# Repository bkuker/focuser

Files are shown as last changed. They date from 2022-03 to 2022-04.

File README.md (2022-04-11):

# Focuser

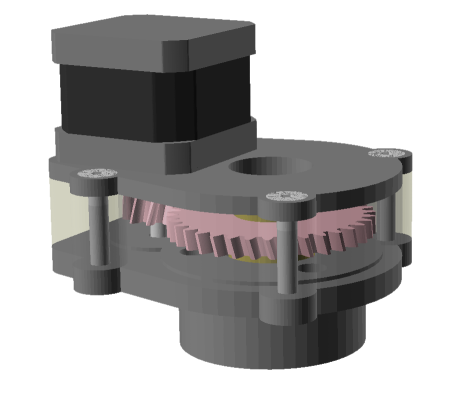
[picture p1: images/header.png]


A 3d printable focuser for Celestron 11" and Moonlite compatible firmware for arduino.

# Hardware

3d Printable, requires NEMA 17 stepper & m3 screws, 30mm M5 flat head screws, thin m5 nuts nuts.

Prints in 6 parts with no support. top and bottom are each printed in two parts and glued together. The only overhangs are the countersinks on top, they print reliably with no support. For all parts I suggest hotter than normal bed temp (70C for PLA) and no brim. Set the printer to leave the bed hot when done, and cover the part with something insulating like a hand towel before turning off the bed heat. Letting the part soak up the heat from the bed, followed by slow even cooling, zero warpage!

# Software

Adapted from https://www.andico.org/2014/04/arduino-based-motor-focuser-controller.html

I forget what I changed and why.

# Libraries

The following libraries are used:

* AccelStepper by Mike McCauley
* NopSCADlib
* Gears Library for OpenSCAD by janssen86.

They are included in this repo for ease of use.

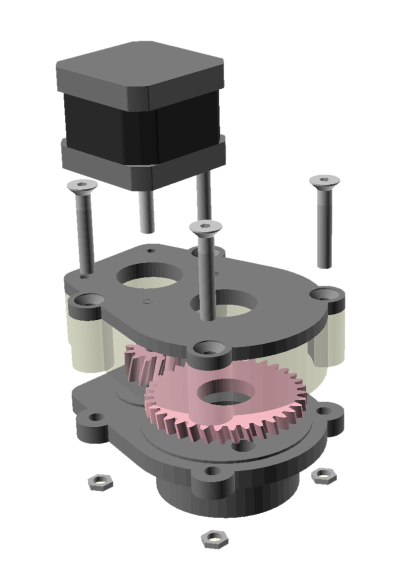
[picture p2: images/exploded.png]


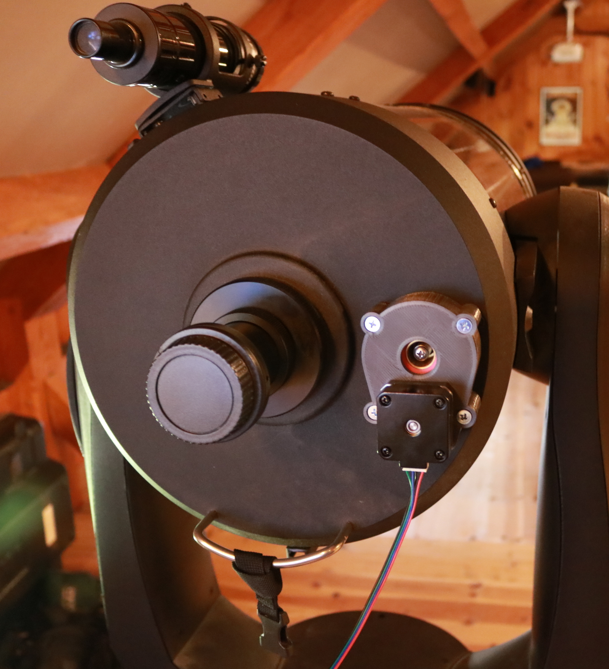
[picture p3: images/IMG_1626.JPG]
In Use


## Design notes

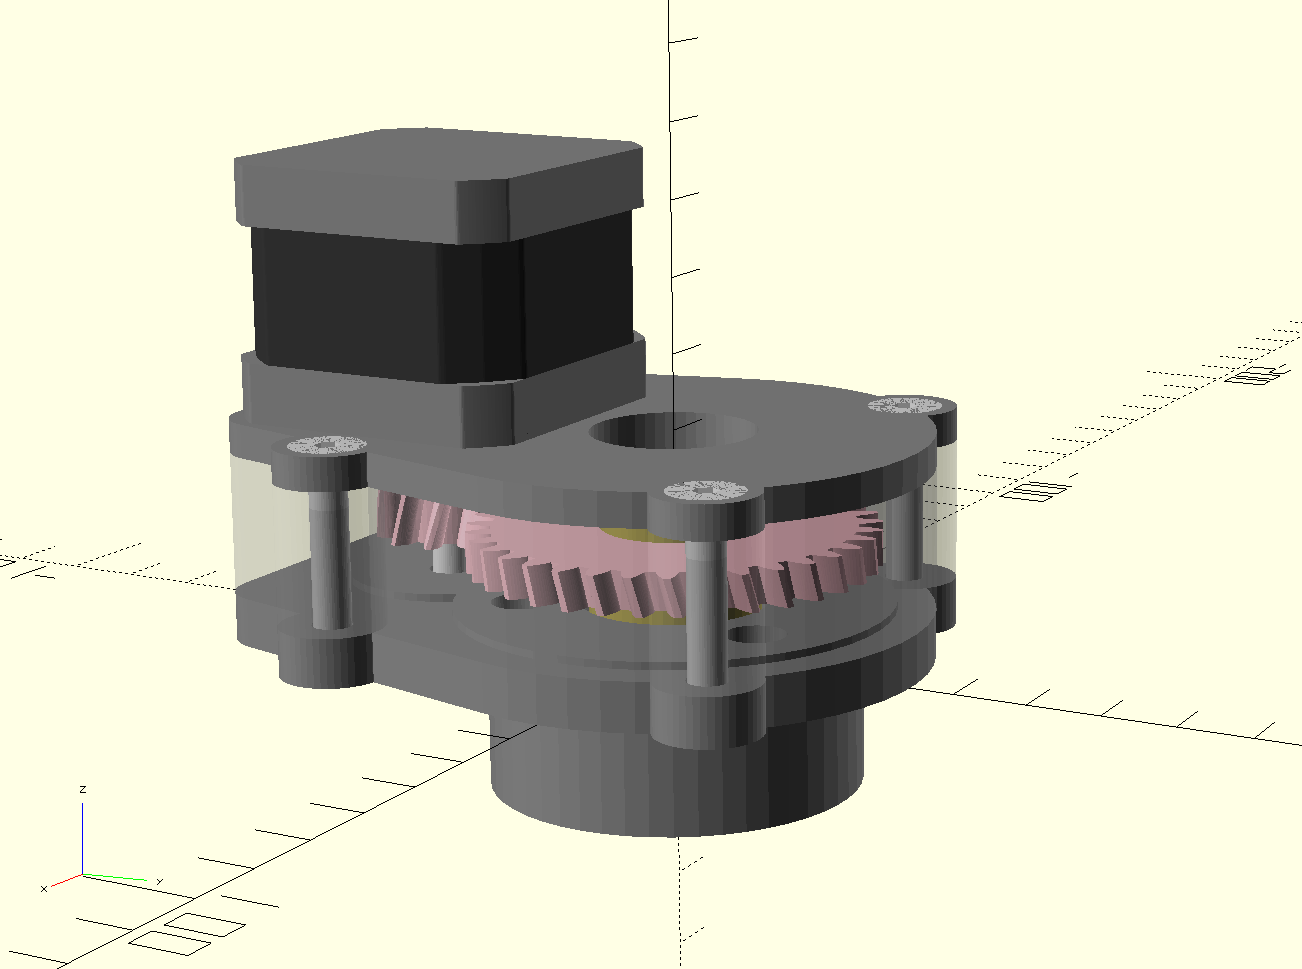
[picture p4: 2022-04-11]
images/Screenshot 2022-04-11 095923.png

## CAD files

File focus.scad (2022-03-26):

include <libraries/NopSCADlib-e5a38b37b3bf3278dea1beb750950f22401af77d/lib.scad>
include <libraries/gears/gears.scad>

NEMA17SB = ["NEMA17S", 42.3, 20, 53.6/2, 25, 11, 2, 5, 20, 31, [8, 8], 3, false, false, 0, 0];

module bosses(){
    //translate([27,20,0])
        //children();
    translate([-27,20,0])
        children();
    translate([27,-35,0])
        children();
}

module screws(){
    translate([0,0,30]){
        bosses(){
            screw(M5_cs_cap_screw, 30);
            translate([0,0,-30])
                scale([1,1,.5])
                    nut(M5_nut);
        }
    }
}

module screws_clearance(){
    translate([0,0,30]){
        bosses(){
            translate([0,0,-.1])
                screw_countersink(M5_cs_cap_screw, drilled = false);
            translate([0,0,.1])
                screw_countersink(M5_cs_cap_screw, drilled = false);
            translate([0,0,-32])
                cylinder(35,2.55,2.55);
            translate([0,0,-31.5])
                    nut(M5_nut);
        }
    }
}

t=4;
module outside(){
    union(){
        bosses(){
            cylinder(1, 7, 7, false);
        }
        hull(){
            cylinder(1, 30+t, 30+t, false);
            translate([0,-34.9,0]){
                cylinder(1, 12+t, 12+t, false);
                rotate([0,0,180])
                    NEMA_screw_positions(NEMA17SB, n = 2)
                        cylinder(1,7,7);
            }
        }
    }
}

module inside(){
    union(){
       cylinder(1, 29.5, 29.5, false);
        translate([0,-34.9,0])
            cylinder(1, 14, 14, false);
    }
}


module base(){
    difference(){
        scale([1,1,6.5])
            outside();

        translate([0,0,-1]){
            cylinder(3.5, 49/2, 49/2, false);
            for ( a = [0, 120, 240] )
                rotate([0,0,a])
                    translate([-20,0,0])
                        cylinder(50, 2,2, true);
            cylinder(50, 25/2,25/2, true);
        }

        screws_clearance();
        
        translate([0,-34.9,0-1]){
            cylinder(50, 3, 3, true);
        }
    }
}

module shell(){
    difference(){
        translate([0,0,6.5])
            scale([1,1,19])
                outside();
        
        scale([1,1,27])
            inside();
        
        screws_clearance();
    }
}

module top(){
    difference(){
        translate([0,0,25.5]){
            difference(){
                union(){
                    scale([1,1,4.5])
                        outside();
                    translate([0,0,-1])
                        inside();
                }
                translate([0,-34.9,4.5]){
                    rotate([0,180,0]){
                        NEMA(NEMA17SB);
                        cylinder(10,NEMA_big_hole(NEMA17SB)+.1,NEMA_big_hole(NEMA17SB)+.1);
                        NEMA_screw_positions(NEMA17SB, n = 4)
                            cylinder(5,1.7,1.7);
                        translate([0,0,3])
                            NEMA_screw_positions(NEMA17SB, n = 4)
                                cylinder(5,4,4);
                    }
                }
                translate([0,0,-2])
                    cylinder(20,11,11);
            }
        }
        screws_clearance();
    }
}

module hardware(){
    translate([0,0,25.5])
        translate([0,-34.9,4.5])
            rotate([0,180,180])
                NEMA(NEMA17S);
    screws();
    color("#b5a642"){
        union(){
            cylinder(12.5, 22.5/2, 22.5/2, false);
            cylinder(20, 19.5/2, 19.5/2, false);
        }
    }
}




module gears(){
    ha = 20;
    mod = 1.525;
    translate([0,0,12.5]){
        spur_gear (modul=mod, tooth_number=35, width=8, bore=19.5, pressure_angle=20, helix_angle=ha, optimized=false);
    }


    translate([0,-34.9,8.5]){
        rotate([0,0,16.5])
        spur_gear (modul=mod, tooth_number=11, width=15, bore=5, pressure_angle=20, helix_angle=-ha, optimized=false);
    }
}

*hardware();

*gears();

base();
color("cyan", .5){
    shell();
}
color("green", .5){
     top();
}



//pcb(ArduinoNano);

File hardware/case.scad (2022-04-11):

module electronics(){
    translate([0,0,1.4]){
        color("green")
            cube([31,70,2]);
            translate([2.3,70-43-2.5,13])
        color("blue")
            cube([18,43,1.5]);
        color("gray"){
            translate([2.3+18/2-8/2,60,14.5]){
                cube([8,10,4]);
            }
        }
    }
}

*electronics();

    t = 2;
    s=.5;

module case(){
        

    union(){
        difference(){
            translate([-(t+s),-(t+s),-t]){
                cube([33.5+2*s+t*2,70+2*s+t*2,24+t*2]);
            }
            translate([-s,-s,0])
            cube([33.5+2*s,70+2*s,24]);
            
            translate([2.3+18/2-11/2-.25,60,1.5+14.5-5/2-.5]){
                cube([11.5,20,10]);
            }
            
            translate([27, 80, 15])
                rotate([90,0,0])
                    cylinder(20,11.5/2,11.5/2);
            
            translate([(33.5+2*s+t*2)/2-(t+s),0,15])
                cube([12.5,20,6],true);
        }
        
        difference(){
            union(){
                translate([-s,-s,0])
                    cube([2,70,5]);
                translate([30-s*2,0,0])
                    cube([5,70,5]);
            }
            electronics();
        }
        
    }
}

intersection(){
    case();
    cube([100,100,100], true);
}

translate([0,20,0])
    difference(){
        case();
        cube([100,100,100], true);
    }

!translate([(33.5+2*s+t*2)/2-(t+s),-t-s-10,15]){
    difference(){
        rotate([90,0,0])
            cylinder(3,10,11.5/2);
        translate([0,0,-12])
            cube([5,10,20],true);
    }
}
    
    
    
    
    

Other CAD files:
hardware/focus.scad

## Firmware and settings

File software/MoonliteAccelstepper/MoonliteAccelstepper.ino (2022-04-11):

// Moonlite-compatible stepper controller
//
// Uses AccelStepper (http://www.airspayce.com/mikem/arduino/AccelStepper/)
//
// Requires a 10uf - 100uf capacitor between RESET and GND on the motor shield; this prevents the
// Arduino from resetting on connect (via DTR going low).  Without the capacitor, this sketch works
// with the stand-alone Moonlite control program (non-ASCOM) but the ASCOM driver does not detect it.
// Adding the capacitor allows the Arduino to respond quickly enough to the ASCOM driver probe
//
// orly.andico@gmail.com, 13 April 2014

#include "src/AccelStepper/AccelStepper.h"

#include <DallasTemperature.h>

/* Microstepping Settings.
 * Run full 16x microstepping all the time on hardware for smoothing and reducing resonance.
 * 
 * Multiply/devide commanded reported position by microsteps, so every 1 step from software results
 * in 16 microsteps. Driver is reset on startup to ensure we always stop on full steps. This makes
 * the position stay more stable when enabling / disabling the driver whild idle to reduce power
 * usage and stepper heat.
 */
#define MICROSTEPS 16
#define MICROSTEP_MULTIPLIER (half_step?MICROSTEPS:MICROSTEPS*2)

/* The gear ratio of the stepper to focuser. 3 means 3 stepper rotations to one focuser rotation */
#define GEAR_RATIO 3
/* How many steps per full revolution of the motor itself (not including gearing) */
#define NATIVE_STEPS_PER_REV 200
/* How many pulses of the STEP pin for one revolution of gear shaft */
#define STEPS_PER_REV (NATIVE_STEPS_PER_REV * GEAR_RATIO * MICROSTEPS)

/*How many seconds for one rotation of the output in full step mode*/
#define SECONDS_PER_REV 3
#define MAXSPEED (STEPS_PER_REV / SECONDS_PER_REV)
#define ACCELERATION 4000

/*How long wait after motion is stopped to disable stepper */
#define SETTLE_MS 500

/* Stepper pins */
#define DIR_PIN  2
#define STEP_PIN 3
#define ENABLE_PIN 6
#define RESET_PIN 5 //Optional

//Not used, but might be hooked to arduino for lazyness
#define MS3 7
#define MS2 8
#define MS1 9
#define SLEEP_PIN 4

/* Optional feature pins */
//#define ONE_WIRE_BUS 11
#define LED_PIN 10

AccelStepper stepper(1, STEP_PIN, DIR_PIN);

#ifdef ONE_WIRE_BUS
OneWire oneWire(ONE_WIRE_BUS); 
DallasTemperature sensors(&oneWire);
DeviceAddress thermometer;
#endif


//Input Handling
#define MAXCOMMAND 8
char inChar;
char cmd[MAXCOMMAND];
char param[MAXCOMMAND];
char line[MAXCOMMAND];
int eoc = 0;
int idx = 0;

//Internal State
int lastTemp = 0;
long millisLastTemp = 0;
long millisLastMove = 0;

//Moonlite State
long pos;
int speed = 2;
int half_step = 0;
int light = 255;

void setup()
{  
  Serial.begin(9600);
  
  stepper.setMaxSpeed(MAXSPEED);
  stepper.setAcceleration(ACCELERATION);
  stepper.disableOutputs();
  stepper.setEnablePin(ENABLE_PIN);
  stepper.setPinsInverted(true,false,true);
  memset(line, 0, MAXCOMMAND);
  millisLastMove = millis();

#ifdef LED_PIN
  analogWrite(LED_PIN, light);
#endif

  pinMode(MS1, OUTPUT);
  digitalWrite(MS1, HIGH);
  pinMode(MS2, OUTPUT);
  digitalWrite(MS2, HIGH);
  pinMode(MS3, OUTPUT);
  digitalWrite(MS3, HIGH);
  pinMode(SLEEP_PIN, OUTPUT);
  digitalWrite(SLEEP_PIN, HIGH);

  pinMode(LED_BUILTIN, OUTPUT);
  

#ifdef RESET_PIN
  //Reset driver and pulse it to align to a whole step
  pinMode(RESET_PIN, OUTPUT);
  digitalWrite(RESET_PIN, LOW);
  delay(10);
  digitalWrite(RESET_PIN, HIGH);
  delay(10);
  stepper.enableOutputs();
  delay(10);
  stepper.disableOutputs();
#endif

#ifdef ONE_WIRE_BUS
  //Start up sensors
  sensors.begin();
  sensors.getAddress(thermometer, 0);
  sensors.requestTemperaturesByAddress(thermometer);
  lastTemp = sensors.getTempC(thermometer)*2;
  sensors.setWaitForConversion(false);
#endif
}

void motion(){
  //Motion Controll
  if (stepper.run()) {
    millisLastMove = millis();
  } 
  else {
    // reported on INDI forum that some steppers "stutter" if disableOutputs is done repeatedly
    // over a short interval; hence we only disable the outputs and release the motor some seconds
    // after movement has stopped
    if ((millis() - millisLastMove) > SETTLE_MS) {
       stepper.disableOutputs();
    }
  }
}


void loop(){
  motion();

  if (stepper.run()) {
    digitalWrite(LED_BUILTIN, bitRead(millis(), 7));
  } else {
    digitalWrite(LED_BUILTIN, bitRead(millis(), 9));
  }
  //Read One Character from serial
  if (Serial.available()) {
    inChar = Serial.read();
    if (inChar != '#' && inChar != ':') {
      line[idx++] = inChar;
      if (idx >= MAXCOMMAND) {
        idx = MAXCOMMAND - 1;
      }
    } 
    else {
      if (inChar == '#') {
        eoc = 1;
      }
    }
    motion();
  } // end if (!Serial.available())

  // process the command we got
  if (eoc) {
    memset(cmd, 0, MAXCOMMAND);
    memset(param, 0, MAXCOMMAND);

    int len = strlen(line);
    if (len >= 2) {
      strncpy(cmd, line, 2);
    }

    if (len > 2) {
      strncpy(param, line + 2, len - 2);
    }

    memset(line, 0, MAXCOMMAND);
    eoc = 0;
    idx = 0;

    // the stand-alone program sends :C# :GB# on startup
    // :C# is a temperature conversion, doesn't require any response

    // LED backlight value, always return "00"
    if (!strcasecmp(cmd, "GB")) {
      Serial.print("00#");
    }

    // home the motor, hard-coded, ignore parameters since we only have one motor
    if (!strcasecmp(cmd, "PH")) { 
      stepper.setCurrentPosition(100);
      stepper.moveTo(0);
    }

    // firmware value, always return "10"
    if (!strcasecmp(cmd, "GV")) {
      Serial.print("10#");
    }

    // get the current motor position
    if (!strcasecmp(cmd, "GP")) {
      pos = stepper.currentPosition() / MICROSTEP_MULTIPLIER;
      char tempString[6];
      sprintf(tempString, "%04X", pos);
      Serial.print(tempString);
      Serial.print("#");
    }

    // get the new motor position (target)
    if (!strcasecmp(cmd, "GN")) {
      pos = stepper.targetPosition() / MICROSTEP_MULTIPLIER;
      char tempString[6];
      sprintf(tempString, "%04X", pos);
      Serial.print(tempString);
      Serial.print("#");
    }

    // get the current temperature
    // The temperature is sent in .5 *C units
    if (!strcasecmp(cmd, "GT")) {
#ifdef ONE_WIRE_BUS
    if ((millis() - millisLastTemp) > 1000 && !stepper.distanceToGo() ) {
      lastTemp = sensors.getTempC(thermometer)*2;
      motion();
      sensors.requestTemperaturesByAddress(thermometer);
      millisLastTemp = millis();
    }
#endif
      char tempString[6];
      sprintf(tempString, "%04X", lastTemp);
      Serial.print(tempString);
      Serial.print("#");
    }

    // get the temperature coefficient, hard-coded
    if (!strcasecmp(cmd, "GC")) {
      Serial.print("02#");
    }

    // get the current light
    if (!strcasecmp(cmd, "GB")) {
      char tempString[6];
      sprintf(tempString, "%02X", light);
      Serial.print(tempString);
      Serial.print("#");
    }

    //set the light
    if (!strcasecmp(cmd, "SB")) {
      light = hexstr2long(param);
#ifdef LED_PIN
      analogWrite(LED_PIN, light);
#endif
    }
    
    // get the current motor speed, only values of 02, 04, 08, 10, 20
    if (!strcasecmp(cmd, "GD")) {
      char tempString[6];
      sprintf(tempString, "%02X", speed);
      Serial.print(tempString);
      Serial.print("#");
    }

    // set speed, only acceptable values are 02, 04, 08, 10, 20
    if (!strcasecmp(cmd, "SD")) {
      speed = hexstr2long(param);
      //Setting the speed too close to the end causes accelstepper to
      //overshoot when moving positive, and freak out when moving negative
      if ( abs(stepper.distanceToGo()) > 20 ){
        stepper.setMaxSpeed(MAXSPEED * 2L / speed);
      }
    }

    /* Get half-stepping */
    if (!strcasecmp(cmd, "GH")) {
      if (half_step) {
        Serial.print("FF#");
      } else {
        Serial.print("00#");
      }
    }

    // motor is moving - 01 if moving, 00 otherwise
    if (!strcasecmp(cmd, "GI")) {
      if (abs(stepper.distanceToGo()) > 0) {
        Serial.print("01#");
      } 
      else {
        Serial.print("00#");
      }
    }

    // set current motor position
    if (!strcasecmp(cmd, "SP")) {
      pos = hexstr2long(param);
      stepper.setCurrentPosition(pos * MICROSTEP_MULTIPLIER);
    }

    // set new motor position
    if (!strcasecmp(cmd, "SN")) {
      pos = hexstr2long(param);
      stepper.moveTo(pos * MICROSTEP_MULTIPLIER);
    }

    /* Set half-step mode */
    if (!strcasecmp(cmd, "SH")) {
        half_step = 1;
    }

    /* Set full-step mode */
    if (!strcasecmp(cmd, "SF")) {
        half_step = 0;
    }

    //Actually start the move
    if (!strcasecmp(cmd, "FG")) {
      stepper.setMaxSpeed(MAXSPEED * 2L / speed);
      stepper.enableOutputs();
      delay(1);
    }

    // stop a move
    if (!strcasecmp(cmd, "FQ")) {
      stepper.moveTo(stepper.currentPosition());
      stepper.setMaxSpeed(1);
      stepper.disableOutputs();
    }

  }
} // end loop

long hexstr2long(char *line) {
  long ret = 0;

  ret = strtol(line, NULL, 16);
  return (ret);
}
